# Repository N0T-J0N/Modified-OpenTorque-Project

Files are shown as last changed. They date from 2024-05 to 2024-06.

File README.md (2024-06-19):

# Modified-OpenTorque-Project

## Table of Contents

1. [Introduction](#1-introduction)  
2. [Methodology](#2-methodology)
- 2.1. [3D-Printing Methodology](#31-3d-printing-methodology)
- 2.2. [ODrive Methodology](#32-odrive-methodology)
- 2.3. [Physical Testing Methodology](#33-physical-testing-methodology)
3. [Results](#3-results)
4. [Future Work](#4-future-work)
5. [Usage](#4-usage)
6. [References](#6-references)
7. [Acknowledgements](#7-acknowledgements)

## 1. Introduction
The OpenTorque project [1] is a robotic actuator developed for legged robots originally by Gabrael Levine and updated [2] by user acisre. The construction of the actuator involves a 100KV brushless DC motor, motor controller, 3D-printed carbon-fiber enclosure, and planetary gearbox. According to the original creator, the actuator performance is summarized in the table below:

| Amperage | Holding Torque (Nm) |
| --- | --- |
| 10  | 7 |
| 30 | 14  |
| 60 | 28  |

According to tests performed by another user Skyentific [3], the actuator performance is summarized in the table below:

| Amperage | Holding Torque (Nm) |
| --- | --- |
| 10  | 6.5727 |
| 20 | 13.2435 |
| 30 | 19.1295 |
| 40 | 25.3098 |

Additionally, for both tests, the motor was able to hold 20 lbs on a 12-inch lever arm. Due to the age of the OpenTorque project, many original parts have been discontinued, therefore parts have been replaced. Parts which have been replaced include the original motor, encoder, and motor controller. The picture below displays the CAD model of the newly modified OpenTorque actuator:

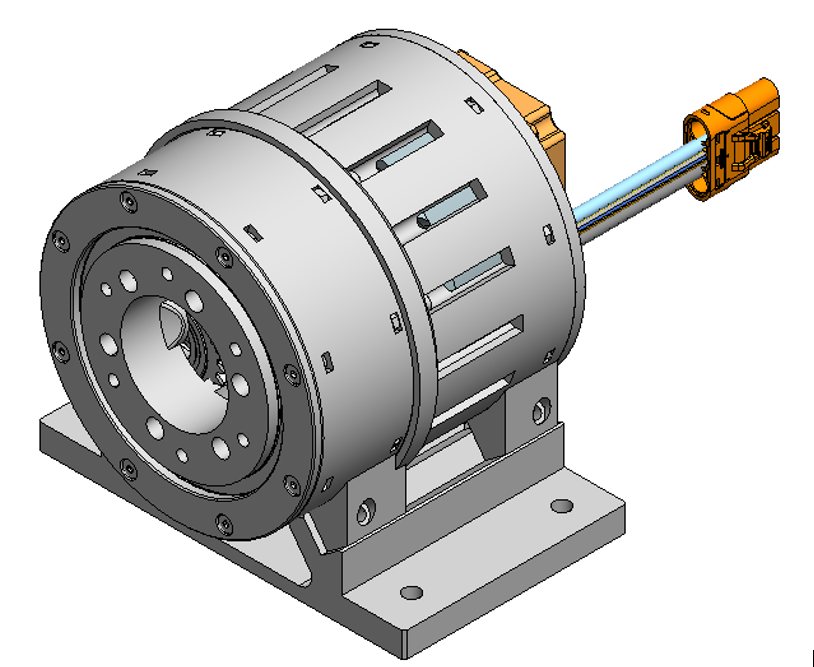
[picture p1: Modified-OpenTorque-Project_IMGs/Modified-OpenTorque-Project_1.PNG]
Modified-OpenTorque-Project_1


Due to the modified structure, motor, encoder, and controller, the actuator must be retested to determine the actual torque output of the actuator. 

## 2. Methodology
## 2.1. 3D-Printing Methodology
Robotic actuators generally experience great force and strain during operation, therefore strong materials should be used during manufacturing to ensure components do not break during operation. To keep the original vision of the original creator (3D-printed parts), and because the construction of the gearbox and housing is complex, carbon-fiber (CF) based filaments were applied during the manufacturing of the modified OpenTorque actuator. The table below summarizes manufacturer characteristics [4] of all applied CF based filaments compared to standard PLA:

| | PLA | PLA-CF | PA6-CF |
| --- | --- | --- | --- |
| Impact Strength – XY (kJ/m^2)  | 26.6 | 23.2 | 40.3 |
| Bending Strength – XY (MPa) | 76 | 89 | 151 |
| Bending Modulus – XY (MPa) | 2750 | 3950 | 5460 |
| Impact Strength – Z (kJ/m^2) | 13.8 | 7.8 | 15.5 |

CF based filaments are generally stronger than standard filaments. Since 3D-printed components and moving gearboxes are difficult to conduct force simulations upon, the following decision tree was applied when selecting filaments for components:

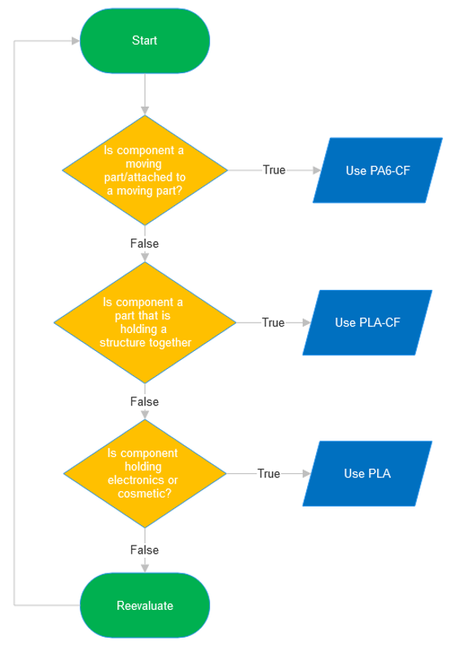
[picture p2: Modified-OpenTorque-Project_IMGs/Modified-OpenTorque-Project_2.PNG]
Modified-OpenTorque-Project_2


Generally, with moving components, the toughest filaments are advisable to prevent wear during continuous use. Wear may cause the moving components (gearbox) to fail and may lead to reduced actuator performance. Tougher filaments (PLA-CF) are advisable on structural but not moving components to ensure stiffness. PLA is acceptable on electronic or cosmetic components to save cost since these parts do not generally experience force and strain. All 3D-print settings and components are included within the given 3MF files. 

## 2.2. ODrive Methodology
Robotic actuators require a controller and encoder to control the position, velocity, and torque of the actuator. The chosen controller-encoder combo is the ODrive S1. The ODrive S1 [5] is an accurate FOC controller capable of control with ROS or Arduino MCUs, and natively uses position, velocity, and torque control. During the construction of the modified OpenTorque actuator, 48V was applied DC- and DC+ using a MEAN WELL LRS-350-48 dedicated power supply. Pins A, B, and C were connected to the respective wire on the chosen 100KV motor (*note, where plug in does not matter). Thermistor wires from the motor were connected to the corresponding pins on the ODrive S1. R- and R+ were connected to opposite ends of the given brake resistor. To connect the ODrive S1 for programming, a USB isolator was used to prevent accidental electrical damage to a programming computer. 

Once physically connected, the ODrive S1 was connected to the ODrive GUI. The following settings were applied to safely operate the actuator:

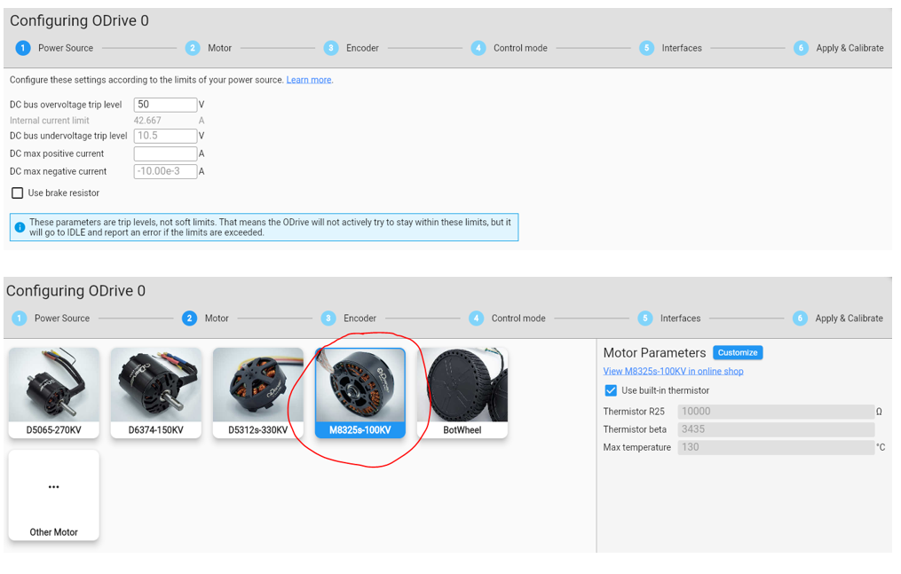
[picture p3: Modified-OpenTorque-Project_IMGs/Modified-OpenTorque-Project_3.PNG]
Modified-OpenTorque-Project_3

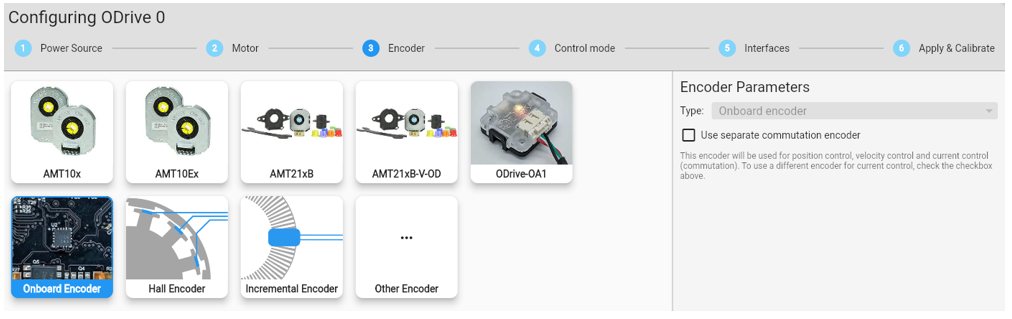
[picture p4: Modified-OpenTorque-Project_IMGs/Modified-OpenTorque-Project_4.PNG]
Modified-OpenTorque-Project_4

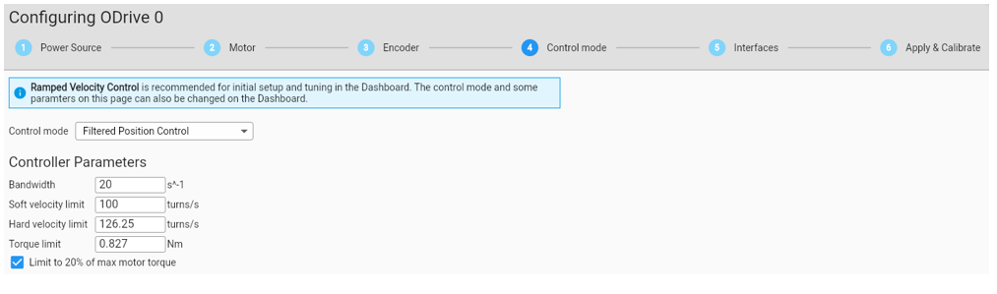
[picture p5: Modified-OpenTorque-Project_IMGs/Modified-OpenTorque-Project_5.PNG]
Modified-OpenTorque-Project_5


All settings are applied to safely operate the actuator. Once settings were set, a calibration sequence was performed, and the dashboard was accessed to manually control position, velocity, and torque. Removing safety will likely increase the performance of the actuator. 

## 2.3. Physical Testing Methodology
To test the maximum torque output of the modified OpenTorque actuator, force must be applied to the center of a scale set to kg by an arm of known length. Force may be applied using the position or torque control functionality through the dashboard. The following equation should be used to calculate the torque output of the OpenTorque actuator:

9.81  *  scale_reading(kg)  *  arm_length(m)  =  torque(Nm)

The following experimental setup was used to determine torque:

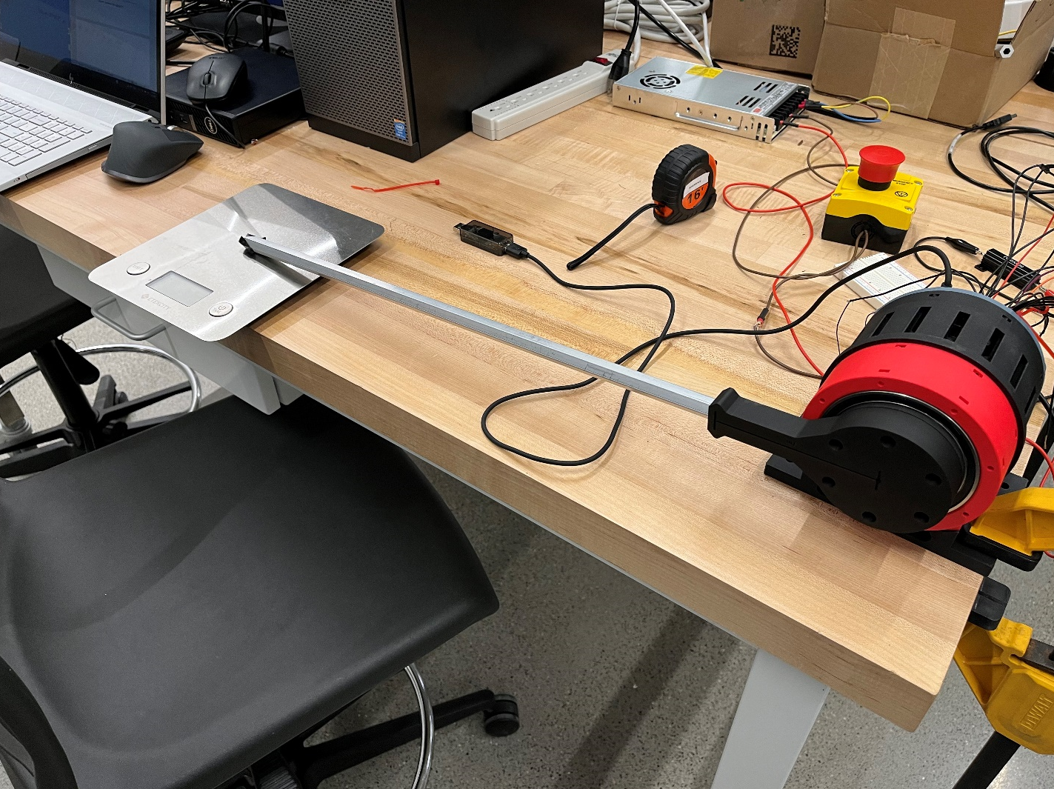
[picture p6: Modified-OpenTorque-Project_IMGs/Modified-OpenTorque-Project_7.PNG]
Modified-OpenTorque-Project_7


## 3. Results
Based on torque testing, the following values were obtained:

| Amperage | Holding Torque (Nm) |
| --- | --- |
| 42.777  | 24.7 |
| 80 | ??? |

| Amperage | Gabrael Levine OpenTorque | Skyentific OpenTorque | Modified OpenTorque |
| --- | --- | --- | --- |
| 10 | 7 | 	6.5727	| - | 
| 20 | - | 13.2435 | - | 
| 30 | 	14 | 19.1295 | - | 
| 40 | - | 25.3098 | 24.7 | 
| 50 | - | - | - | 
| 60 | 	28 | - | - | 
| 70 | - | - | - | 
| 80 | - | - | ??? | 

The picture displays the position, velocity, and current graphs during the maximum torque test using position control. The limit of approximately 40A was reached during the test, which is displayed in the current vs time graph. If “DC bus overvoltage trip-level” was set to 24V instead of 50V and a 24V supply was used instead of a 48V supply, the internal current limit would increase to 80A and likely increase maximum torque while reducing velocity. Additionally, if the torque was not limited to 20% of the maximum value, the torque value could increase when operating using torque control mode. 

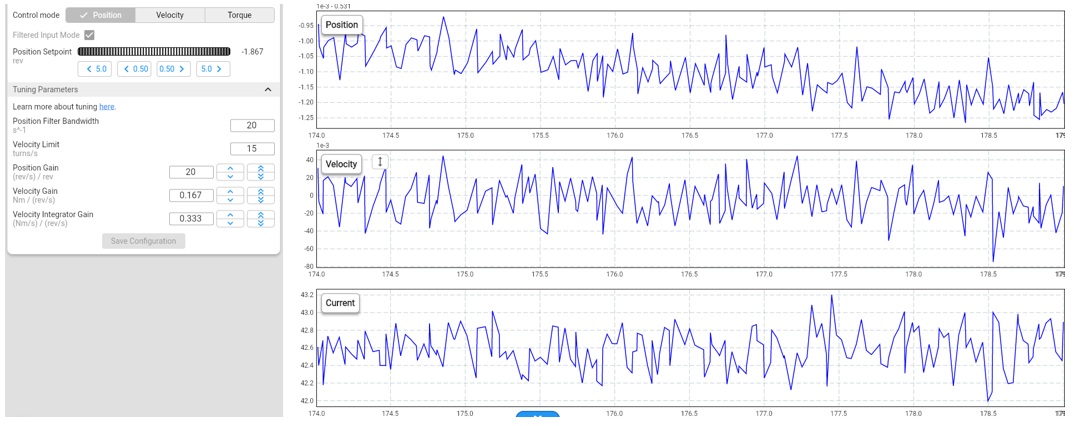
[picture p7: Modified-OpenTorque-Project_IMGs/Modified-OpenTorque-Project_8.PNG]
Modified-OpenTorque-Project_8

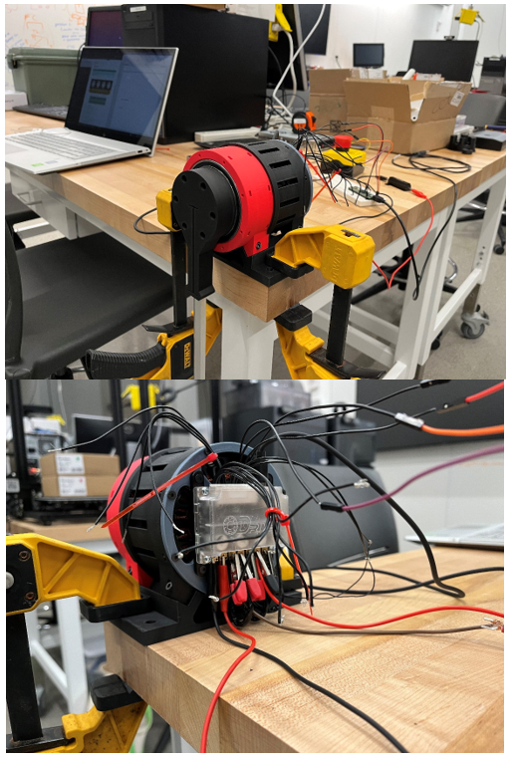
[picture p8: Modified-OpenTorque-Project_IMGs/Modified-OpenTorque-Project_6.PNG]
Modified-OpenTorque-Project_6


## 4. Future Work
Future tests of this actuator should involve implementing a 24V supply to increase the current limit to 80A. Implementing the increased amperage should involve temperature tests during operation, since the motor will likely increase in temperature, causing a reduction in performance. 

## 5. Usage
To make your own Modified OpenTorque actuator, you should buy the [equipment](/Modified-OpenTorque_PO/Modified-OpenTorque_Equipment_PO.xlsx) using the given PO, then buy the components for the [actuator](/Modified-OpenTorque_PO/Modified-OpenTorque_Actuator_PO.xlsx). The assembly follows the [process](https://discourse.odriverobotics.com/t/opentorque-project-new-design/8280) by user acisre. The modified parts of the assembly should be fairly obvious. If you are having trouble, refer to the assembly in the given STEP file.

## 6. References
[1] https://hackaday.io/project/159404-opentorque-actuator

[2] https://discourse.odriverobotics.com/t/opentorque-project-new-design/8280

[3] https://www.youtube.com/watch?v=6lW2YGQQIQ4

[4] https://bambulab.com/en-us/filament-guide

[5] https://docs.odriverobotics.com/v/latest/hardware/s1-datasheet.html

## 7. Acknowledgements
The author acknowledges Logan Forcier for his work on the modified CAD models of the OpenTorque project and Alvin Ye for his work on implementing a Teensy 4.1 and ROS to communicate with the ODrive S1.

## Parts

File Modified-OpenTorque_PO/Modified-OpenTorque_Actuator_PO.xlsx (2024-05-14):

Purchase Request Form
Date: 5/1/2024
Requester Name | Chair Approval | Dean Approval | Fund | Org | Sub-Account | Split | Funding Total
Jonathan Ho |  |  |  |  |  |  | $0.00
Requester Name | Chair Approval | Dean Approval | Fund | Org | Sub-Account | Split | Requisition total
 |  |  |  |  |  |  | $444.48
Number | Vendor Name | Item Type | Quantity | Cost Per Unit | Total Cost | Notes | Link
1 | Odrive | ODrive S1 | 1 | $149.00 | $149.00 | Select "Screw Terminals" | https://odriverobotics.com/shop/odrive-s1
2 | ODrive | Enclosure for ODrive S1 | 1 | $9.00 | $9.00 | Select "3D-Printed Cover" and Black | https://odriverobotics.com/shop/enclosure-for-odrive-s1
3 | ODrive | Harness Build Kit For ODrive S1 | 1 | $9.00 | $9.00 |  | https://odriverobotics.com/shop/harness-build-kit-for-odrive-s1
4 | ODrive | Heat Spreader Plate for ODrive S1 | 1 | $12.00 | $12.00 |  | https://odriverobotics.com/shop/heat-spreader-plate-for-odrive-s1
5 | ODrive | Motor with encoder magnet - M8325s 100KV | 1 | $149.00 | $149.00 |  | https://odriverobotics.com/shop/m8325s
6 | Amazon | 6902-2RS Deep Groove Ball Bearing | 1 | $13.99 | $13.99 |  | https://www.amazon.com/6902-2RS-Bearing-15x28x7mm-61902RS-Bearings/dp/B08L7SS7P3
7 | Amazon | 6814-2RS Deep Groove Ball Bearing | 2 | $12.29 | $24.58 |  | https://www.amazon.com/Bettomshin-6814-2RS-Bearing-70x90x10mm-Bearings/dp/B08XNCGNX4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
8 | McMaster | Alloy Steel Socket Head Screw, Black-Oxide, M3 x 0.5 mm Thread, 20 mm Long | 1 | $13.59 | $13.59 |  | https://www.mcmaster.com/91290A123/
9 | McMaster | Black-Oxide Steel Hex Nut, Medium-Strength, Class 8, M3 x 0.5 mm Thread | 1 | $11.38 | $11.38 |  | https://www.mcmaster.com/90593A001/
10 | McMaster | Black-Oxide Alloy Steel Hex Drive Flat Head Screw, 90 Degree Countersink, M3 x 0.50 mm Thread, 20 mm Long | 1 | $11.03 | $11.03 |  | https://www.mcmaster.com/91294A136/
11 | McMaster | Black-Oxide Alloy Steel Hex Drive Flat Head Screw, 90 Degree Countersink, M3 x 0.50 mm Thread, 10 mm Long | 1 | $6.36 | $6.36 |  | https://www.mcmaster.com/91294A130/
12 | McMaster | Alloy Steel Socket Head Screw, Black-Oxide, M3 x 0.5 mm Thread, 10 mm Long | 1 | $9.54 | $9.54 |  | https://www.mcmaster.com/91290A115/
13 | McMaster | Alloy Steel Socket Head Screw, Black-Oxide, M4 x 0.7 mm Thread, 20 mm Long | 1 | $13.59 | $13.59 |  | https://www.mcmaster.com/91290A168/
14 | McMaster | Black-Oxide Steel Hex Nut, Medium-Strength, Class 8, M4 x 0.7 mm Thread | 1 | $12.42 | $12.42 |  | https://www.mcmaster.com/90593A003/
 |  |  |  |  | $444.48
1 |  |  |  |  | $0.00
2 |  |  |  |  | $0.00
3 |  |  |  |  | $0.00
4 |  |  |  |  | $0.00
5 |  |  |  |  | $0.00
6 |  |  |  |  | $0.00
7 |  |  |  |  | $0.00
8 |  |  |  |  | $0.00
9 |  |  |  |  | $0.00
10 |  |  |  |  | $0.00
 |  |  |  |  | $0.00
1 |  |  |  |  | $0.00
2 |  |  |  |  | $0.00
3 |  |  |  |  | $0.00
4 |  |  |  |  | $0.00
5 |  |  |  |  | $0.00
6 |  |  |  |  | $0.00
7 |  |  |  |  | $0.00
8 |  |  |  |  | $0.00
9 |  |  |  |  | $0.00
10 |  |  |  |  | $0.00
 |  |  |  |  | $0.00

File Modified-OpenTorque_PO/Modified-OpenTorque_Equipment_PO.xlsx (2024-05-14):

Purchase Request Form
Date: 5/1/2024
Requester Name | Chair Approval | Dean Approval | Fund | Org | Sub-Account | Split | Funding Total
Jonathan Ho |  |  |  |  |  |  | $0.00
Requester Name | Chair Approval | Dean Approval | Fund | Org | Sub-Account | Split | Requisition total
 |  |  |  |  |  |  | $124.19
Number | Vendor Name | Item Type | Quantity | Cost Per Unit | Total Cost | Notes | Link
1 | McMaster | Emergency Stop Enclosed Push-Button Switch | 1 | $75.28 | $75.28 |  | https://www.mcmaster.com/6785K21
2 | Amazon | MEAN WELL LRS-350-48 350.4W 48V 7.3 Amp Single Output Switchable Power Supply | 1 | $32.91 | $32.91 |  | https://www.amazon.com/MEAN-WELL-LRS-350-48-350-4W-Switchable/dp/B013EU4KNK
3 | ODrive | USB-C to USB-A Cable and USB Isolator for ODrive Pro/S1 | 1 | $16.00 | $16.00 |  | https://odriverobotics.com/shop/usb-c-to-usb-a-cable-and-usb-isolator
 |  |  |  |  | $124.19
1 |  |  |  |  | $0.00
2 |  |  |  |  | $0.00
3 |  |  |  |  | $0.00
4 |  |  |  |  | $0.00
5 |  |  |  |  | $0.00
6 |  |  |  |  | $0.00
7 |  |  |  |  | $0.00
8 |  |  |  |  | $0.00
9 |  |  |  |  | $0.00
10 |  |  |  |  | $0.00
 |  |  |  |  | $0.00
1 |  |  |  |  | $0.00
2 |  |  |  |  | $0.00
3 |  |  |  |  | $0.00
4 |  |  |  |  | $0.00
5 |  |  |  |  | $0.00
6 |  |  |  |  | $0.00
7 |  |  |  |  | $0.00
8 |  |  |  |  | $0.00
9 |  |  |  |  | $0.00
10 |  |  |  |  | $0.00
 |  |  |  |  | $0.00

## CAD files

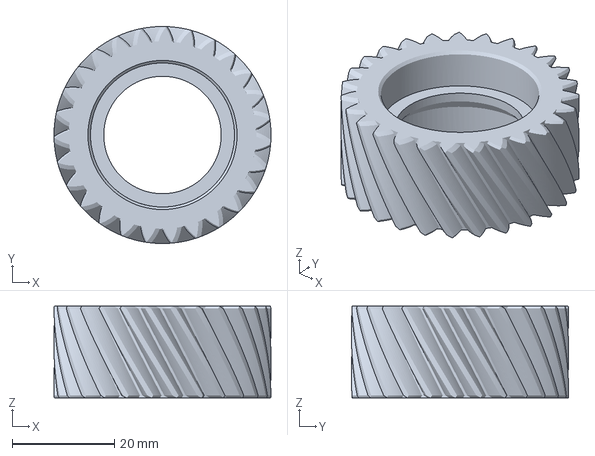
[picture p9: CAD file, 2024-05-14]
Modified-OpenTorque-3D-Prints/OpenTorque_Planet_Gear.3mf
42.5 x 42.5 x 18.0 mm

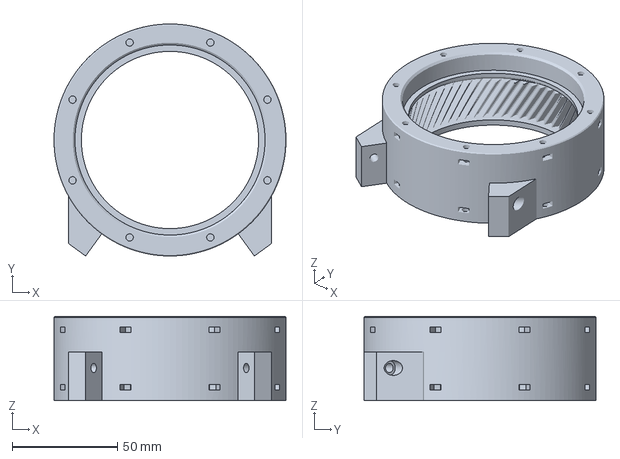
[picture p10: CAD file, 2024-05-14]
Modified-OpenTorque-3D-Prints/OpenTorque_Ring_Gear.3mf
110.0 x 110.0 x 40.0 mm

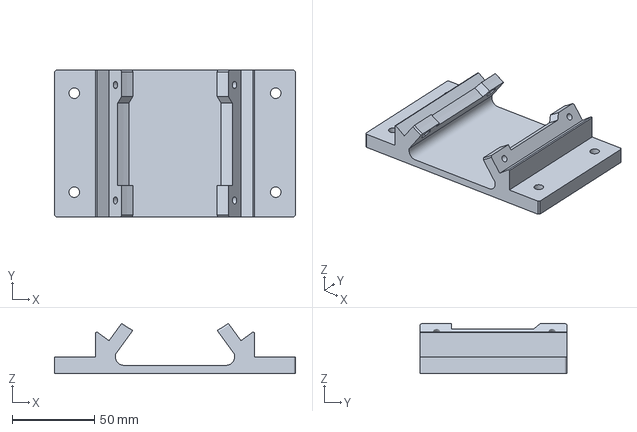
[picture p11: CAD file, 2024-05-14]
Modified-OpenTorque-3D-Prints/OpenTorque_Stand.3mf
146.1 x 89.0 x 30.4 mm

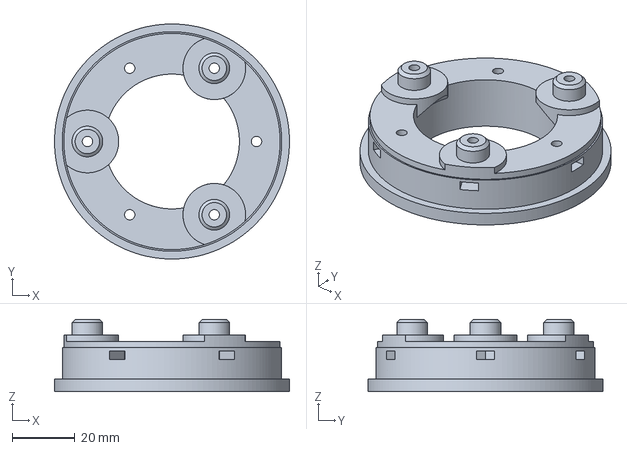
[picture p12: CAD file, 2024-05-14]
Modified-OpenTorque-3D-Prints/OpenTorque_Planet_Carrier_Back.3mf
75.0 x 75.0 x 23.0 mm

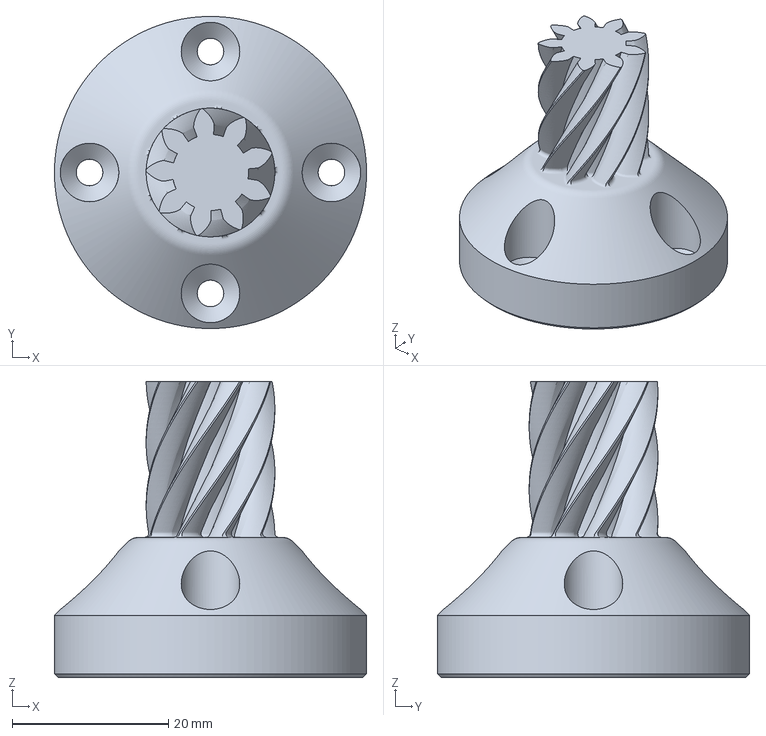
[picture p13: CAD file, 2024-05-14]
Modified-OpenTorque-3D-Prints/OpenTorque_Sun_Gear.3mf
40.0 x 40.0 x 38.0 mm

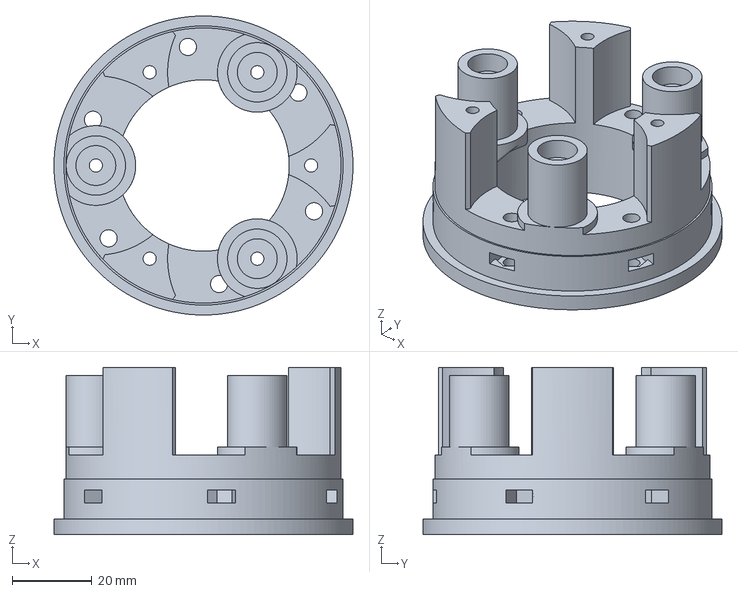
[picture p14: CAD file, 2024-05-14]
Modified-OpenTorque-3D-Prints/OpenTorque_Planet_Carrier_Front.3mf
75.0 x 75.0 x 42.0 mm

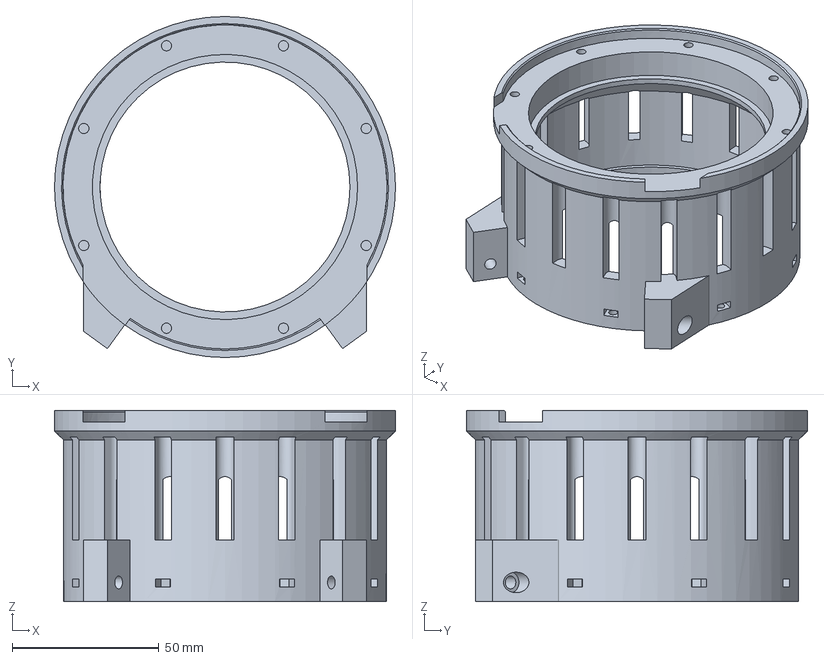
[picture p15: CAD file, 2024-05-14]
Modified-OpenTorque-3D-Prints/OpenTorque_Housing.3mf
116.0 x 116.0 x 65.0 mm

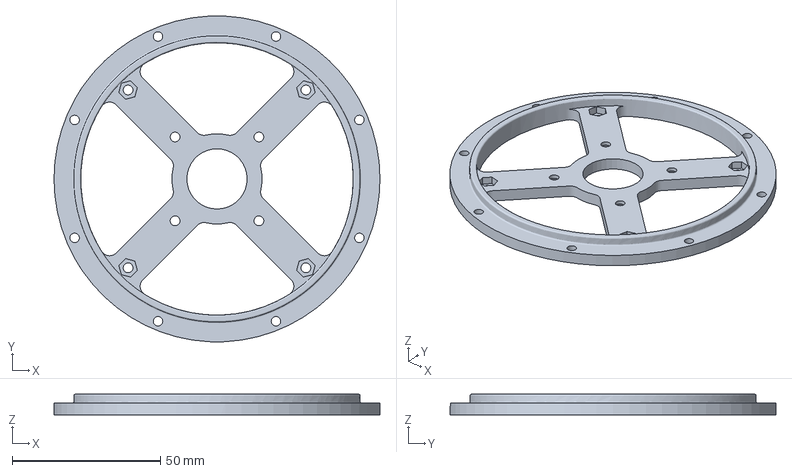
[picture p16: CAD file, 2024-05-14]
Modified-OpenTorque-3D-Prints/OpenTorque_Backplate.3mf
110.0 x 109.9 x 7.00 mm
